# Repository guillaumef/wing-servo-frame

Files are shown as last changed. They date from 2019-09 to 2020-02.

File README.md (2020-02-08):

# wing-servo-frame

Wing servo frame - fully parametric - arms/bearing - servo database

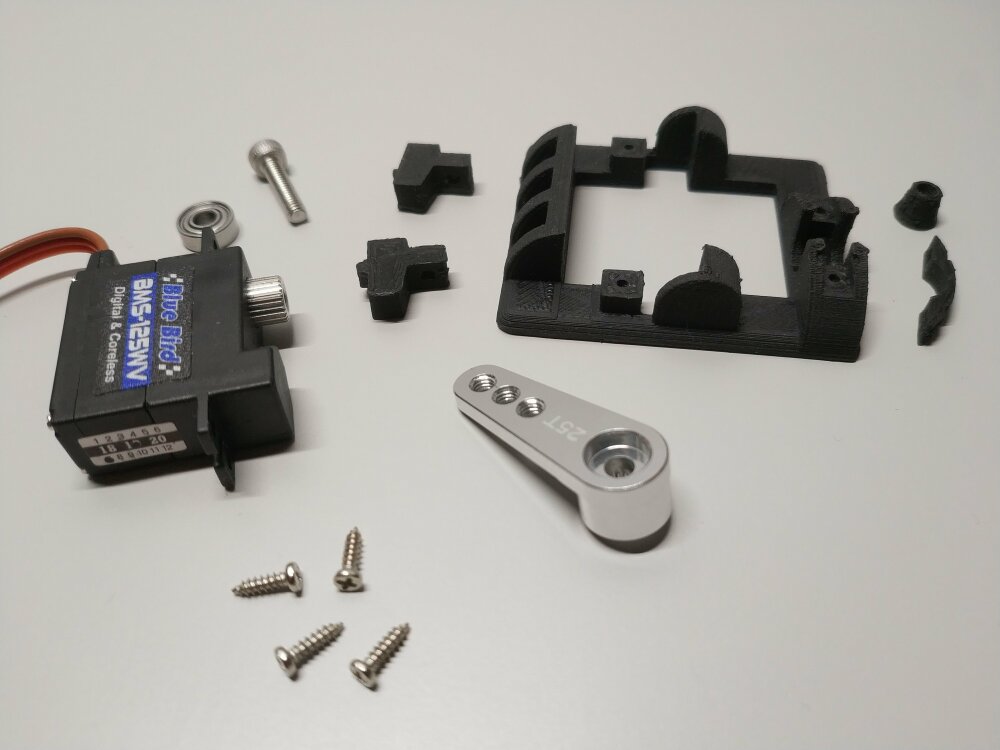
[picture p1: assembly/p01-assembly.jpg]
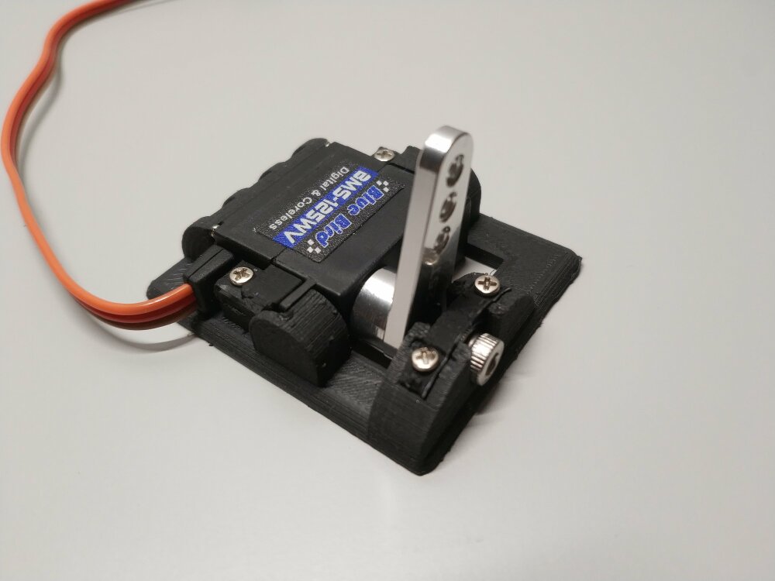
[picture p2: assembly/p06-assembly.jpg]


Videos (KST X08N, Bluebird BMS-125WV):

[](https://youtu.be/2ph3OZgdkxs) [](https://youtu.be/XQHXTqi7j4g)

[All animated gifs](GIFSHOW.md)

### Project description

- all servo ears format
- parametric servo dimensions
- parametric bearing dimensions (like: MR83ZZ -> MR95ZZ ...)
- with or without external bearing (also with parametric bearing dimensions), left/right/both sides
- for horizontal ears, manage ear notch, screws or both
- many options (general thickness, arm clearance, frame round factor, mode light, ...)
- no added height to the servo thickness

### Directories/files

- servo-frame.scad : OpenScad code and embedded documentation
- configuration.scad : Configuration and constants with embedded documentation
- Makefile : generate the STLs for all known servos
- stls : some auto-generated STLs for each servo in the KB (in some configurations)
- assembly : pictures and video of the assembly

### Usage

You need openscad and a text editor.

```
git clone https://github.com/guillaumef/wing-servo-frame.git
```

- Launch openscad on servo-frame.scad
- Edit the configuration.scad file to fit your needs (openscad preview can be a bit tricked by the complexity, use F6 to render the final version if necessary)
- Generate the STL
- Print...

### Bearing and screw

Both are easy to find, portable and far more cost-effective than commercial products and
proprietary arm screws.

The trivial constraint:
screw diameter (servo arm screw) must be inferior or equal to the bearing internal diameter.

##### Screw

The arm screw is replaced with a longer one.

Nearly all servo arm screws are M2,M2.5,M3.
A dissident is the KST X12, with M2.3 screw (nearly proprietary).
For this one, the simpliest way is a M2.5 tap set (flat tip or make it flatter), you get a strong M2.5 with 3.5mm depth.
You need M2,M2.5,M3 screws with a minimum length of 15mm and you are good to go for any servos.

##### Bearing

The scad file is generating the specified servo arm clearance (space between the
arm and the frame).
It is also generating the bearing shaft except for two special modes:
- if screw diameter is equal to bearing internal diameter: screw is automatically use as bearing shaft
- if screw head diameter is equal to bearing internal diameter: screw head is automatically use as bearing shaft

Bearing price is $2 for 10pcs, $8 for 50pcs... (aliexpress).

The servo frame accepts 8mm bearing even for 8mm servo.

To manage any kind of servos, choose your way:
- To get a full steel shaft, buy a bunch of them with 2mm,2.5mm,3mmm internal diameter. i.e:
  - MR52ZZ (2x5x2.5 mm)
  - 682XZZ (2.5x6x2.6 mm)
  - MR63ZZ (3x6x2.5 mm)
- To get a printed shaft, buy a bunch of 5mm internal diameter. i.e:
  - MR85ZZ (5x8x2.5)

### STLs directory

To ease the process, this directory provides multiple automatically generated STLs in some configurations:
- hollow / solid frame
- bearing: none/left/right/both

The configuration file is provided for each generated stl.
The bearing size is chosen for the best case scenario per servo: screw as the bearing shaft.

### Openscad feedback

The scad file is providing you information feedback on the screw/bearing.
Like this one:
```
ECHO: "******************"
ECHO: "Bearing shaft/arm screw:"
ECHO: "**** the shaft inserted in the bearing is printed"
ECHO: "**** screw length (threaded part) should be approximately between 15.5 and 18.3 mm"
ECHO: "**** >> Tuning the length is possible with the 'frame_arm_clearance' parameter"
ECHO: "**** screw thread metric is M3"
ECHO: "******************"
```
Or:
```
ECHO: "******************"
ECHO: "Bearing shaft/arm screw:"
ECHO: "**** 'arm_screw_dia' matches bearing internal diameter:"
ECHO: "**** >> the screw is the bearing shaft"
ECHO: "**** screw length (threaded part) should be approximately between 14.5 and 17.3 mm"
ECHO: "**** >> Tuning the length is possible with the 'frame_arm_clearance' parameter"
ECHO: "**** screw thread metric is M3"
ECHO: "******************"
```

##### Printing

100% infill, ABS or Nylon material. Small layer printing is better.
On a Ultimaker2, ~ one servo frame per hour in good quality (layer 0.1mm).

### Miscellaneous

- on carbon/fiberglass, use coarse grit sandpaper to roughen up the surfaces and
clean with acetone (NEVER on ABS)
- use a thread-locking fluid for the arm screw.
- for wings, add a strap (1-2mm Fiberglass, carbon) between the wing
top skin and the servo/frame. I quote the "Aeroic Schwing instructions":
This all ensures a ridgedly held servo. Servos that pop off do so because of flex in
the skins. Doing it this way there’s a lot of gluing area and no flex so the servo
cannot pop off. A weak glue joint with an unprepared servo is perfectly adequate.
The servo is held on the top skin, bottom skin and the head is held by the bearing
housing which itself is bonded to both skins! To remove just cut the strap, unbolt
the shaft and twist the servo. It pops out clean! But most of the time it may be you
just need to replace the arm. Then it’s even easier as you just unbolt the shaft and
leave the servo in situ.

### Servo database

If you add new servo dimensions to the list, I will be pleased to include them.
You can provide them via a Github Issue. Thanks!

Servo list:

- MKS DS6100 / HV6100
- MKS DS75K
- MKS DS75K-N
- MKS HV6130
- BlueBird BMS-125WV / BMS-126WV / BMS-127WV
- BlueBird BMS-207WV
- BlueBird BMS-115HV
- BlueBird BMS-A10S
- BlueBird BMS-A10V
- BlueBird BMS-A10H
- KST X12-508 HV
- KST X10 HV / DS125MG / DS225MG
- KST X10 MINI HV / DS135MG
- KST X10-710 HV / DS145MG
- KST X08 HV
- KST X08H HV
- KST X08N HV
- KST X08 Plus HV
- KST X08H Plus HV
- Emax ES3352
- Emax ES08MDII
- TowerPro MG90D 15g

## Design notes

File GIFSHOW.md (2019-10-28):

## BlueBird-BMS-115HV

#### hollow
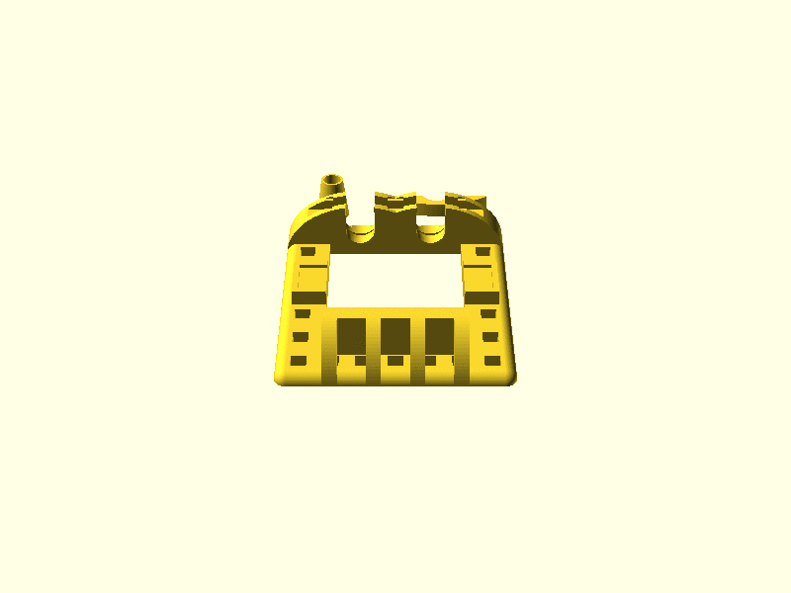
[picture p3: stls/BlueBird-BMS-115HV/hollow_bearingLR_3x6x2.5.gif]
BlueBird-BMS-115HV frame
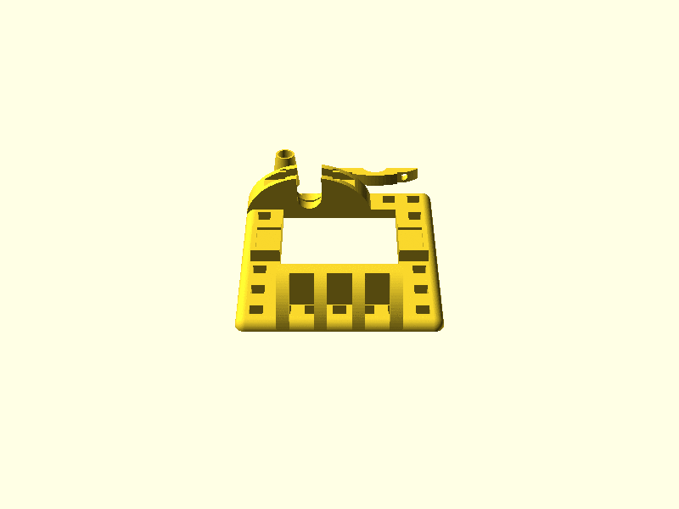
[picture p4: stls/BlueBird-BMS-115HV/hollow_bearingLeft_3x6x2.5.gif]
BlueBird-BMS-115HV frame
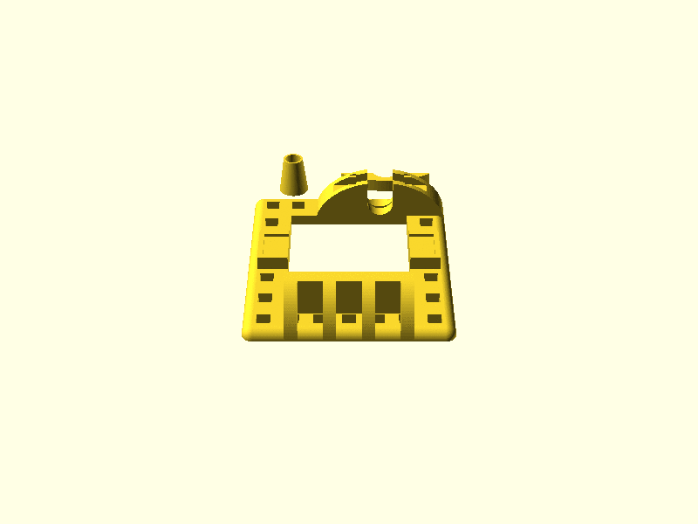
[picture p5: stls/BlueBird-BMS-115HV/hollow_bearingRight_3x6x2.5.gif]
BlueBird-BMS-115HV frame
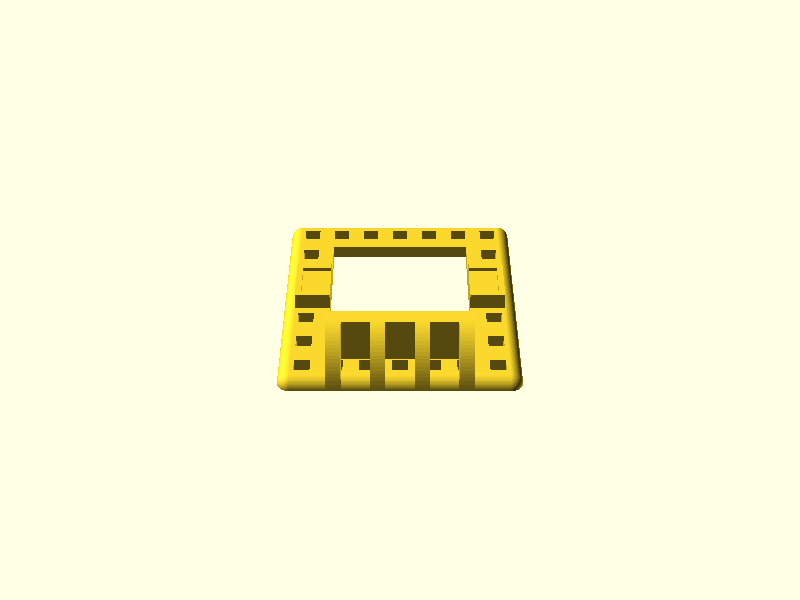
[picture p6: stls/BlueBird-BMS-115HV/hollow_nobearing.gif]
BlueBird-BMS-115HV frame
    
#### solid
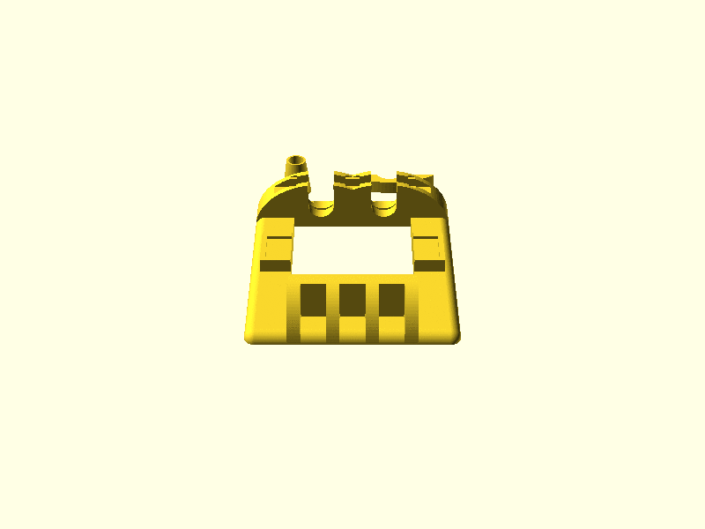
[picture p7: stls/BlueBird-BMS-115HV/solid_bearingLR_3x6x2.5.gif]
BlueBird-BMS-115HV frame
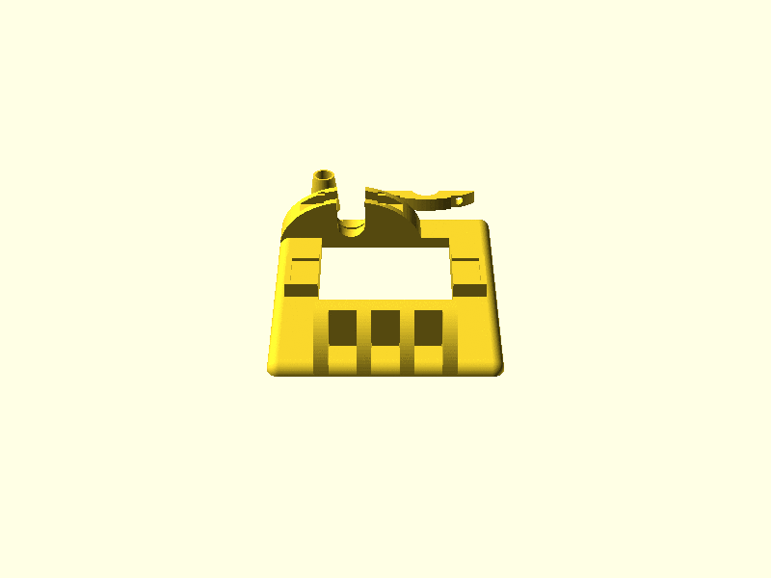
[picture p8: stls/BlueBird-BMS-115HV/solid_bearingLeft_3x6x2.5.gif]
BlueBird-BMS-115HV frame
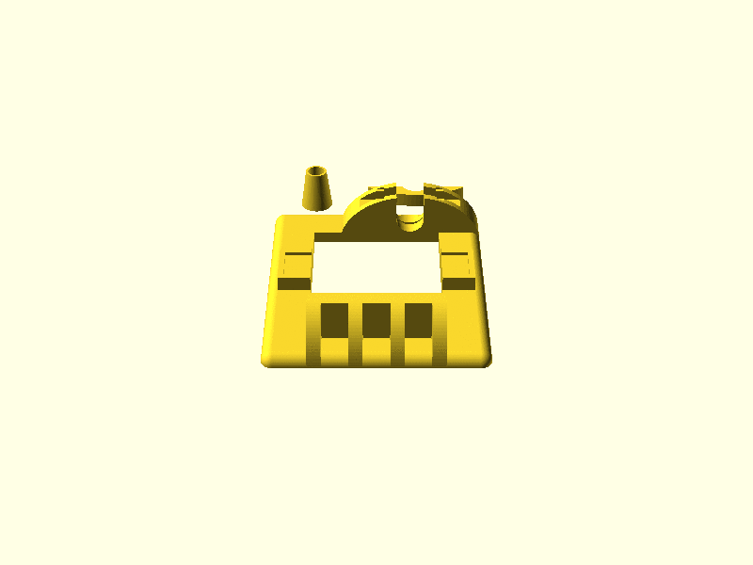
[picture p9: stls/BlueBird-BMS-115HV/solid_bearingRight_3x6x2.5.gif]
BlueBird-BMS-115HV frame
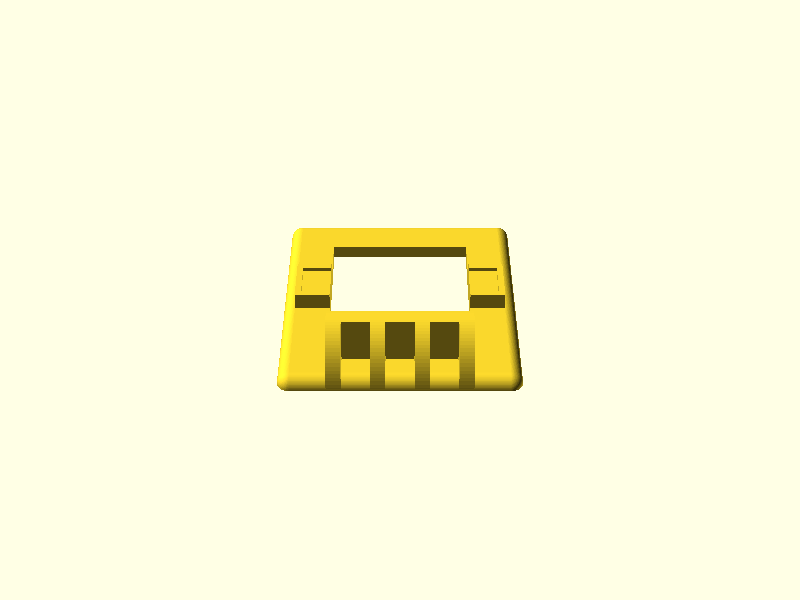
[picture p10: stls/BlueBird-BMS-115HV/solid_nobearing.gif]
BlueBird-BMS-115HV frame
    

## BlueBird-BMS-125WV

#### hollow
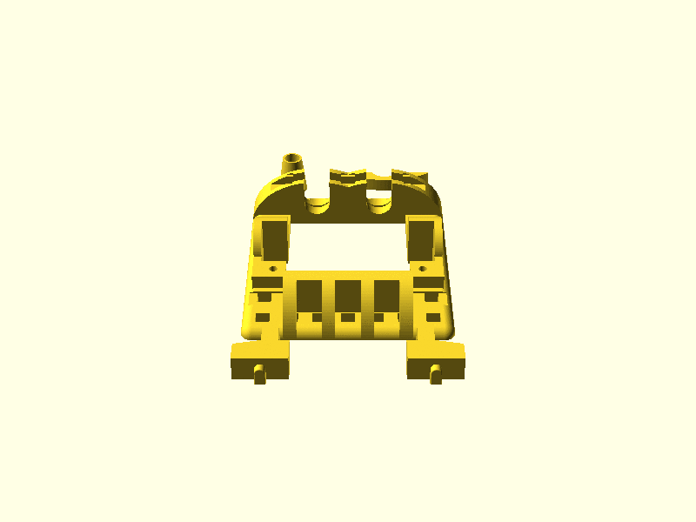
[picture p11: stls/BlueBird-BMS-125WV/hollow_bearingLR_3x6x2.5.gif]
BlueBird-BMS-125WV frame
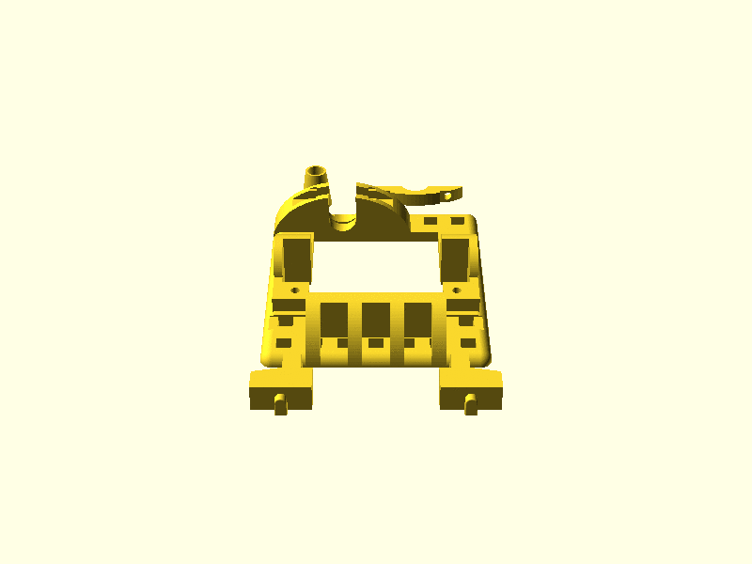
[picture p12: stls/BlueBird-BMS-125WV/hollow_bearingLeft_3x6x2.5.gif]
BlueBird-BMS-125WV frame
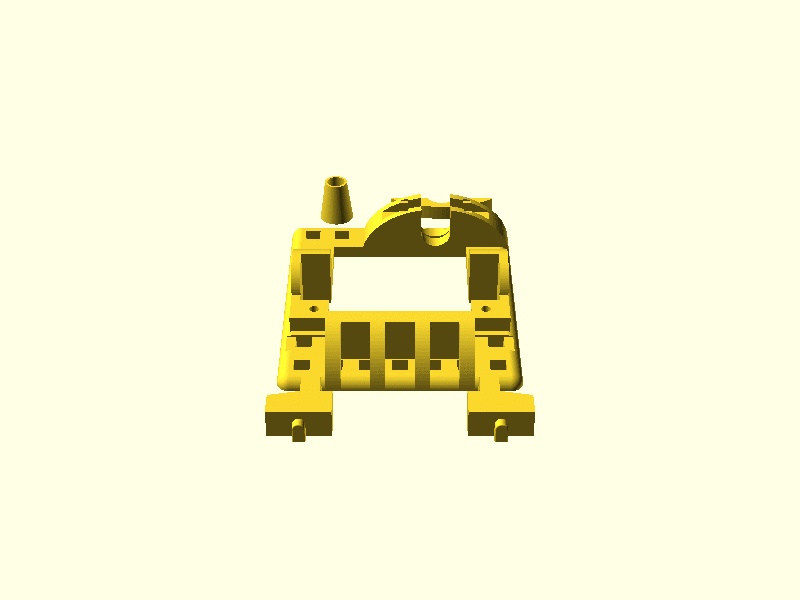
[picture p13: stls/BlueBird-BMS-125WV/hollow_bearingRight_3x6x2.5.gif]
BlueBird-BMS-125WV frame
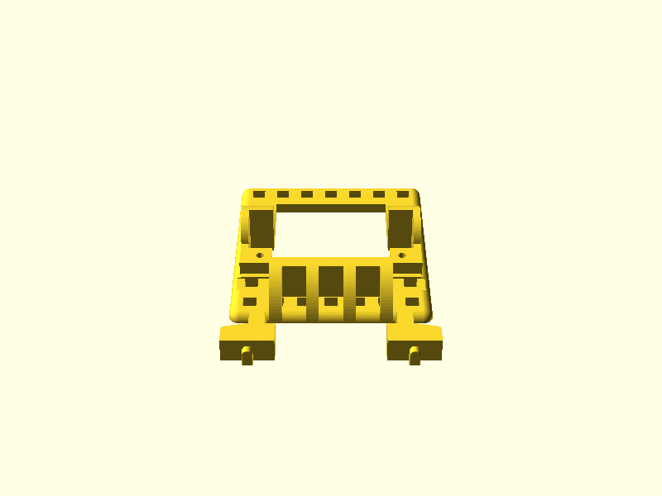
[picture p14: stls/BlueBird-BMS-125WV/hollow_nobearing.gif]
BlueBird-BMS-125WV frame
    
#### solid
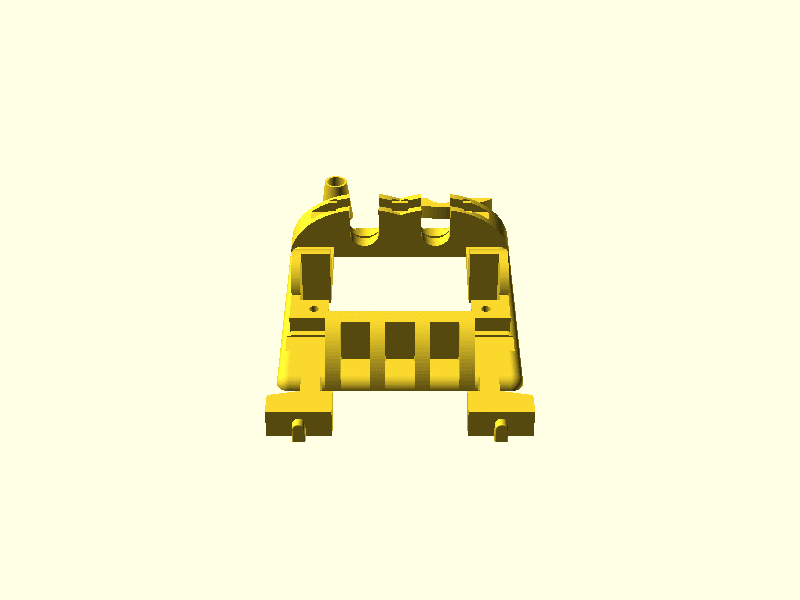
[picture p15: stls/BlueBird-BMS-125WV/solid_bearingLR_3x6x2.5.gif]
BlueBird-BMS-125WV frame
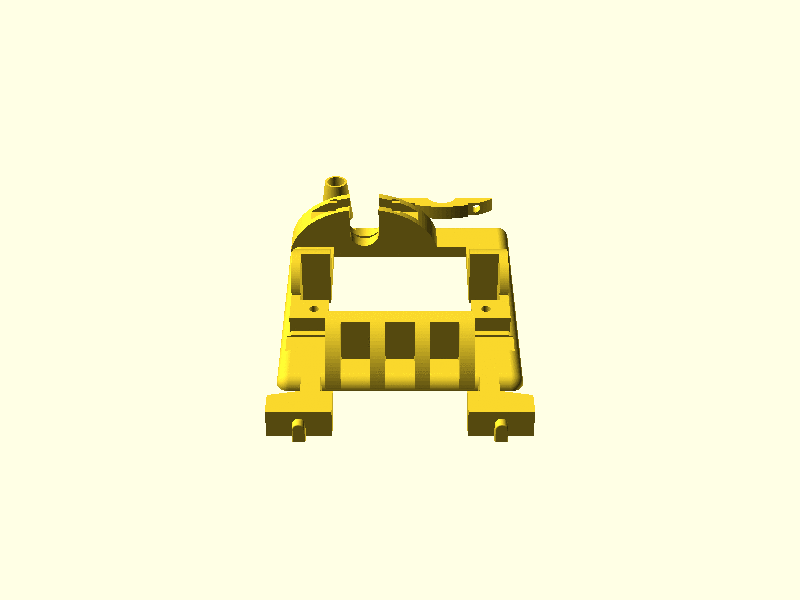
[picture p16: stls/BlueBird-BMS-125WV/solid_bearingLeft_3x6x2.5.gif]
BlueBird-BMS-125WV frame
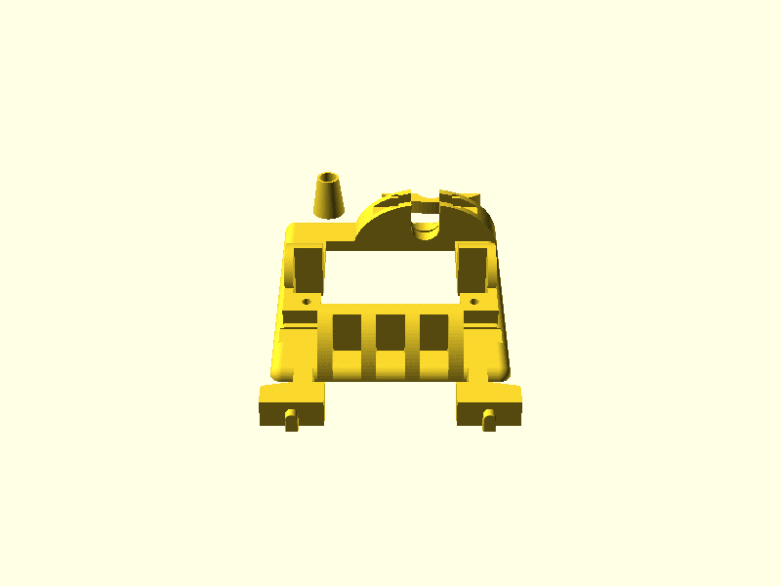
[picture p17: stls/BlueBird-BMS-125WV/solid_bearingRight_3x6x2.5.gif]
BlueBird-BMS-125WV frame
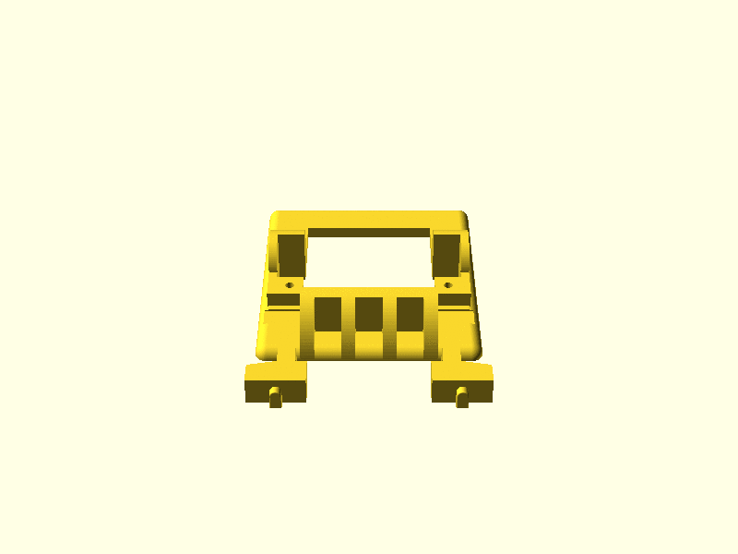
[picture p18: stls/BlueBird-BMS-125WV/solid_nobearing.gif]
BlueBird-BMS-125WV frame
    

## BlueBird-BMS-207WV

#### hollow
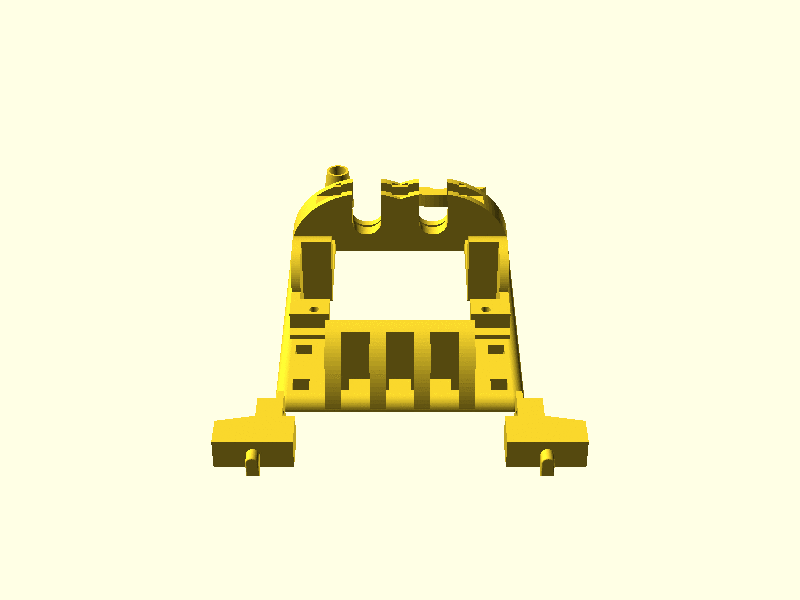
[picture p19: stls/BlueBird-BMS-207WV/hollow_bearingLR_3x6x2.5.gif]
BlueBird-BMS-207WV frame
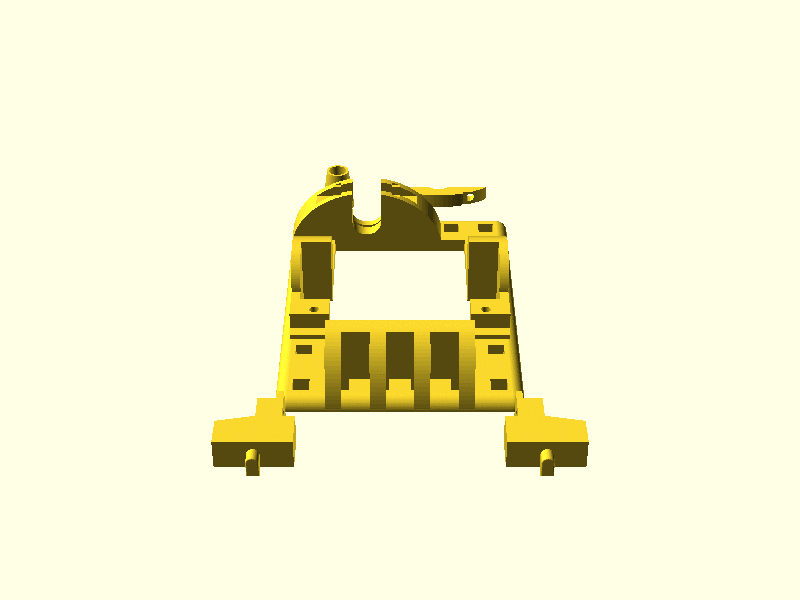
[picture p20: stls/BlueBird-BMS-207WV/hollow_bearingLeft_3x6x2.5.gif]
BlueBird-BMS-207WV frame
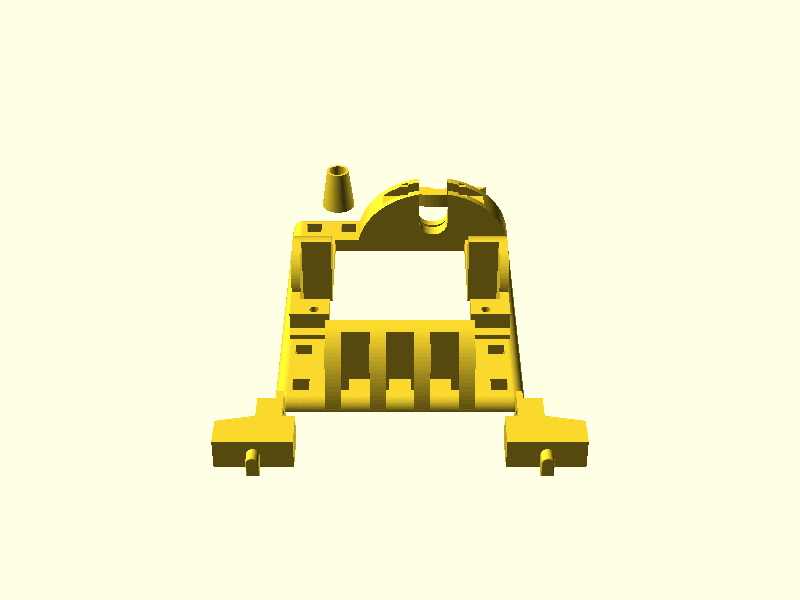
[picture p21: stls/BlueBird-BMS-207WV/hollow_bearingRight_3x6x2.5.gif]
BlueBird-BMS-207WV frame
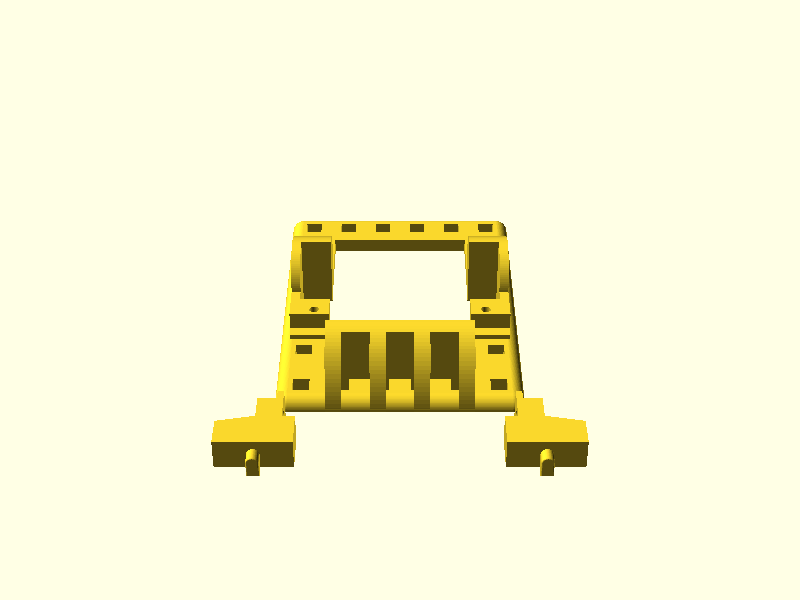
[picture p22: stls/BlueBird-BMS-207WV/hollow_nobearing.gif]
BlueBird-BMS-207WV frame
    
#### solid
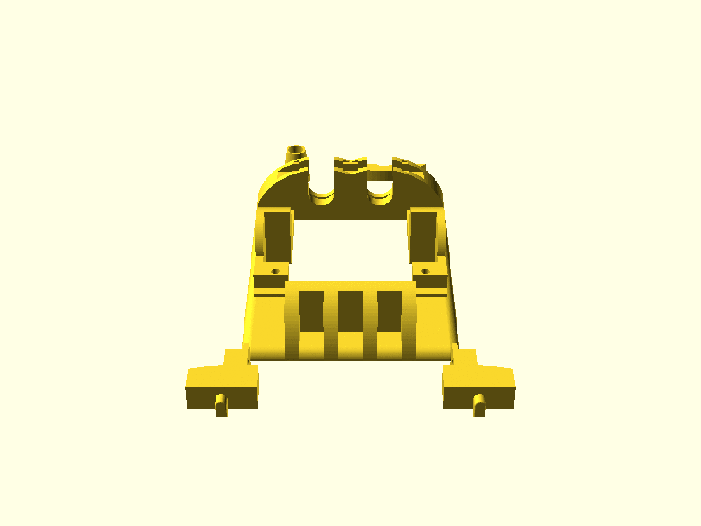
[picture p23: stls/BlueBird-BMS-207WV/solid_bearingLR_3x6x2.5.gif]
BlueBird-BMS-207WV frame
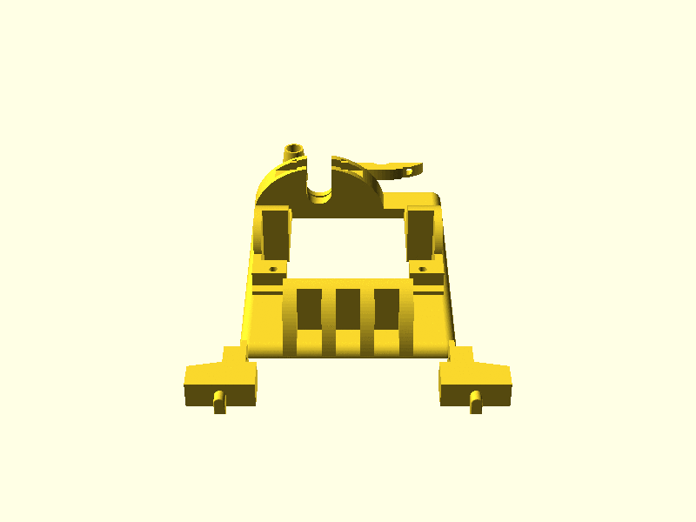
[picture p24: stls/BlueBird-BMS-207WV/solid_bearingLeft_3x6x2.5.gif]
BlueBird-BMS-207WV frame
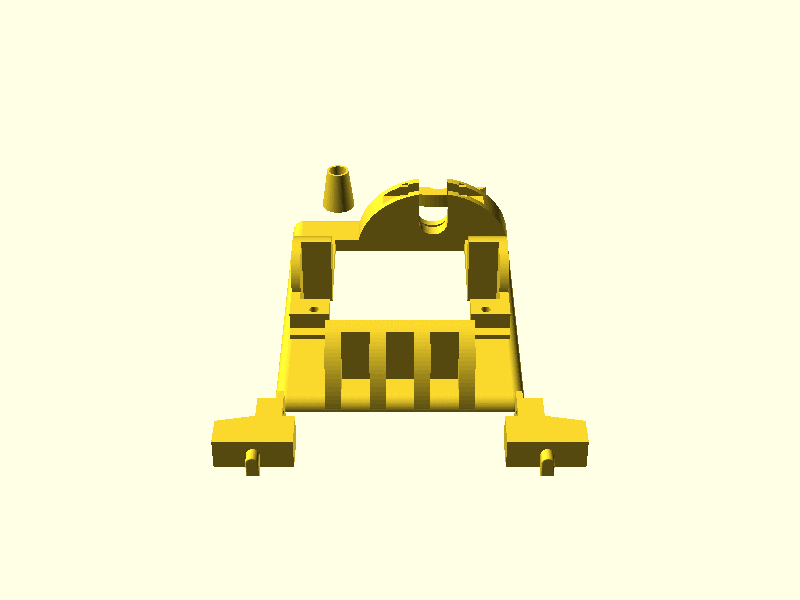
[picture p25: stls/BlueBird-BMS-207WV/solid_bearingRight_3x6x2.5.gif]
BlueBird-BMS-207WV frame
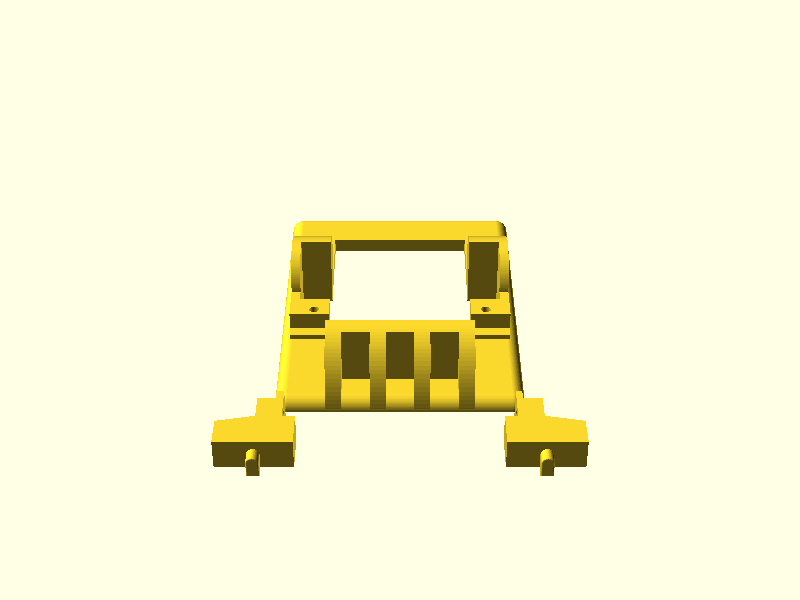
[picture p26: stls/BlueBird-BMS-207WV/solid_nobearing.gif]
BlueBird-BMS-207WV frame
    

## BlueBird-BMS-A10H

#### hollow
BlueBird-BMS-A10H frame BlueBird-BMS-A10H frame BlueBird-BMS-A10H frame BlueBird-BMS-A10H frame 
#### solid
BlueBird-BMS-A10H frame BlueBird-BMS-A10H frame BlueBird-BMS-A10H frame BlueBird-BMS-A10H frame 

## BlueBird-BMS-A10S

#### hollow
BlueBird-BMS-A10S frame BlueBird-BMS-A10S frame BlueBird-BMS-A10S frame BlueBird-BMS-A10S frame 
#### solid
BlueBird-BMS-A10S frame BlueBird-BMS-A10S frame BlueBird-BMS-A10S frame BlueBird-BMS-A10S frame 

## BlueBird-BMS-A10V

#### hollow
BlueBird-BMS-A10V frame BlueBird-BMS-A10V frame BlueBird-BMS-A10V frame BlueBird-BMS-A10V frame 
#### solid
BlueBird-BMS-A10V frame BlueBird-BMS-A10V frame BlueBird-BMS-A10V frame BlueBird-BMS-A10V frame 

## Emax-ES08MDII

#### hollow
Emax-ES08MDII frame Emax-ES08MDII frame Emax-ES08MDII frame Emax-ES08MDII frame 
#### solid
Emax-ES08MDII frame Emax-ES08MDII frame Emax-ES08MDII frame Emax-ES08MDII frame 

## Emax-ES3352

#### hollow
Emax-ES3352 frame Emax-ES3352 frame Emax-ES3352 frame Emax-ES3352 frame 
#### solid
Emax-ES3352 frame Emax-ES3352 frame Emax-ES3352 frame Emax-ES3352 frame 

## KST-X08-HV

#### hollow
KST-X08-HV frame KST-X08-HV frame KST-X08-HV frame KST-X08-HV frame 
#### solid
KST-X08-HV frame KST-X08-HV frame KST-X08-HV frame KST-X08-HV frame 

## KST-X08-Plus-HV

#### hollow
KST-X08-Plus-HV frame KST-X08-Plus-HV frame KST-X08-Plus-HV frame KST-X08-Plus-HV frame 
#### solid
KST-X08-Plus-HV frame KST-X08-Plus-HV frame KST-X08-Plus-HV frame KST-X08-Plus-HV frame 

## KST-X08H-HV

#### hollow
KST-X08H-HV frame KST-X08H-HV frame KST-X08H-HV frame KST-X08H-HV frame 
#### solid
KST-X08H-HV frame KST-X08H-HV frame KST-X08H-HV frame KST-X08H-HV frame 

## KST-X08H-Plus-HV

#### hollow
KST-X08H-Plus-HV frame KST-X08H-Plus-HV frame KST-X08H-Plus-HV frame KST-X08H-Plus-HV frame 
#### solid
KST-X08H-Plus-HV frame KST-X08H-Plus-HV frame KST-X08H-Plus-HV frame KST-X08H-Plus-HV frame 

## KST-X08N-HV

#### hollow
KST-X08N-HV frame KST-X08N-HV frame KST-X08N-HV frame KST-X08N-HV frame 
#### solid
KST-X08N-HV frame KST-X08N-HV frame KST-X08N-HV frame KST-X08N-HV frame 

## KST-X10-710-HV

#### hollow
KST-X10-710-HV frame KST-X10-710-HV frame KST-X10-710-HV frame KST-X10-710-HV frame 
#### solid
KST-X10-710-HV frame KST-X10-710-HV frame KST-X10-710-HV frame KST-X10-710-HV frame 

## KST-X10-HV

#### hollow
KST-X10-HV frame KST-X10-HV frame KST-X10-HV frame KST-X10-HV frame 
#### solid
KST-X10-HV frame KST-X10-HV frame KST-X10-HV frame KST-X10-HV frame 

## KST-X10-MINI-HV

#### hollow
KST-X10-MINI-HV frame KST-X10-MINI-HV frame KST-X10-MINI-HV frame KST-X10-MINI-HV frame 
#### solid
KST-X10-MINI-HV frame KST-X10-MINI-HV frame KST-X10-MINI-HV frame KST-X10-MINI-HV frame 

## KST-X12-508-HV

#### hollow
KST-X12-508-HV frame KST-X12-508-HV frame KST-X12-508-HV frame KST-X12-508-HV frame 
#### solid
KST-X12-508-HV frame KST-X12-508-HV frame KST-X12-508-HV frame KST-X12-508-HV frame 

## MKS-DS6100

#### hollow
MKS-DS6100 frame MKS-DS6100 frame MKS-DS6100 frame MKS-DS6100 frame 
#### solid
MKS-DS6100 frame MKS-DS6100 frame MKS-DS6100 frame MKS-DS6100 frame 

## MKS-DS75K-N

#### hollow
MKS-DS75K-N frame MKS-DS75K-N frame MKS-DS75K-N frame MKS-DS75K-N frame 
#### solid
MKS-DS75K-N frame MKS-DS75K-N frame MKS-DS75K-N frame MKS-DS75K-N frame 

## MKS-DS75K

#### hollow
MKS-DS75K frame MKS-DS75K frame MKS-DS75K frame MKS-DS75K frame 
#### solid
MKS-DS75K frame MKS-DS75K frame MKS-DS75K frame MKS-DS75K frame 

## MKS-HV6130

#### hollow
MKS-HV6130 frame MKS-HV6130 frame MKS-HV6130 frame MKS-HV6130 frame 
#### solid
MKS-HV6130 frame MKS-HV6130 frame MKS-HV6130 frame MKS-HV6130 frame 

## TowerPro-MG90D-15g

#### hollow
TowerPro-MG90D-15g frame TowerPro-MG90D-15g frame TowerPro-MG90D-15g frame TowerPro-MG90D-15g frame 
#### solid
TowerPro-MG90D-15g frame TowerPro-MG90D-15g frame TowerPro-MG90D-15g frame TowerPro-MG90D-15g frame

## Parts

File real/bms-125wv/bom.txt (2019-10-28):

1 x BlueBird BMS-125WV
   ...

1 x MR63ZZ - aliexpress
1 x M3*16 - aliexpress
1 x Servo arm 25T Metal - aliexpress
4 x mini screws for wood/abs - classic micro servo screws

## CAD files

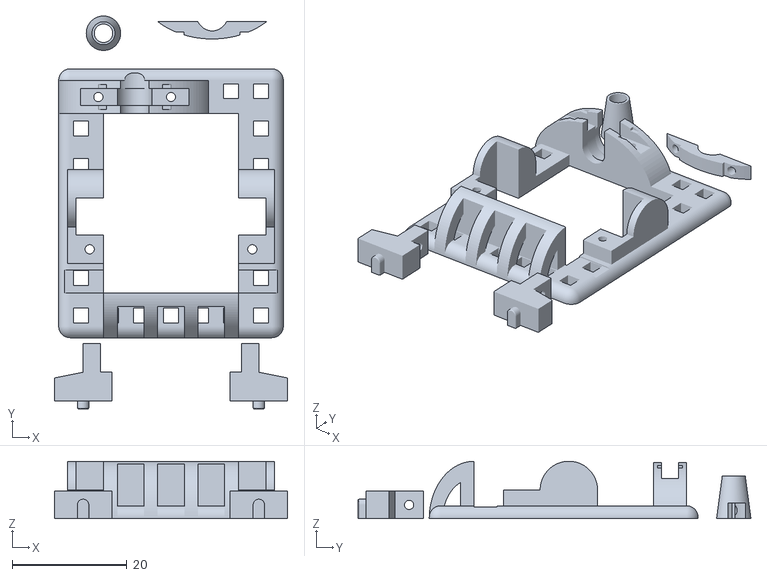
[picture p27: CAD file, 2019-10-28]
real/bms-125wv/model.stl
40.6 x 68.4 x 10.0

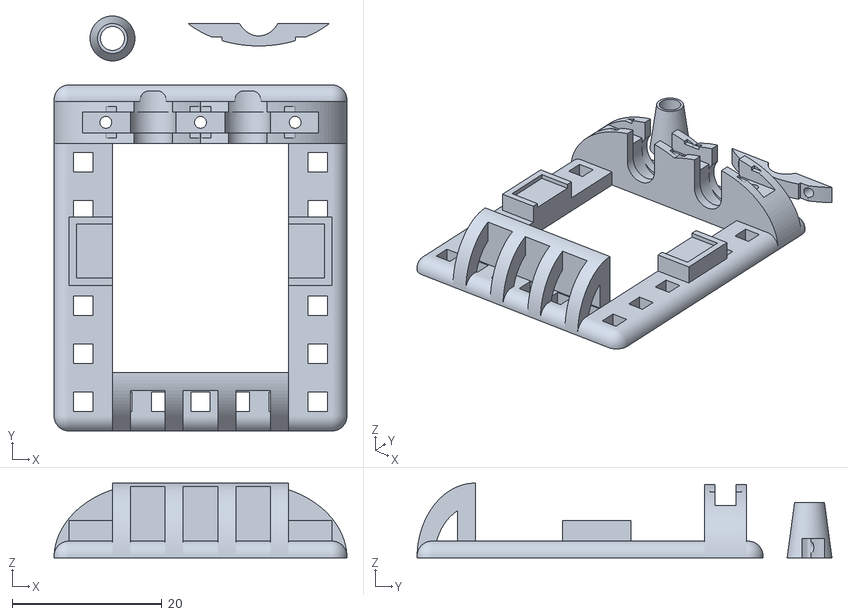
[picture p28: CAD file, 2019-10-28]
stls/BlueBird-BMS-115HV/hollow_bearingLR_3x6x2.5.stl
39.1 x 55.4 x 10.0

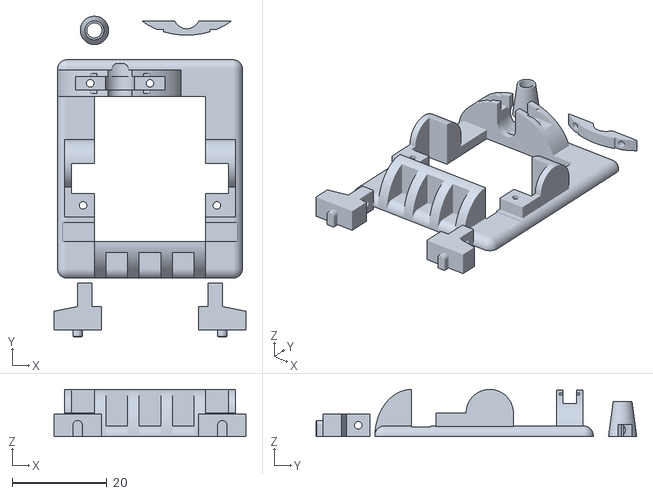
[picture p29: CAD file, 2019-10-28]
stls/BlueBird-BMS-125WV/solid_bearingLeft_3x6x2.5.stl
40.6 x 67.8 x 10.0

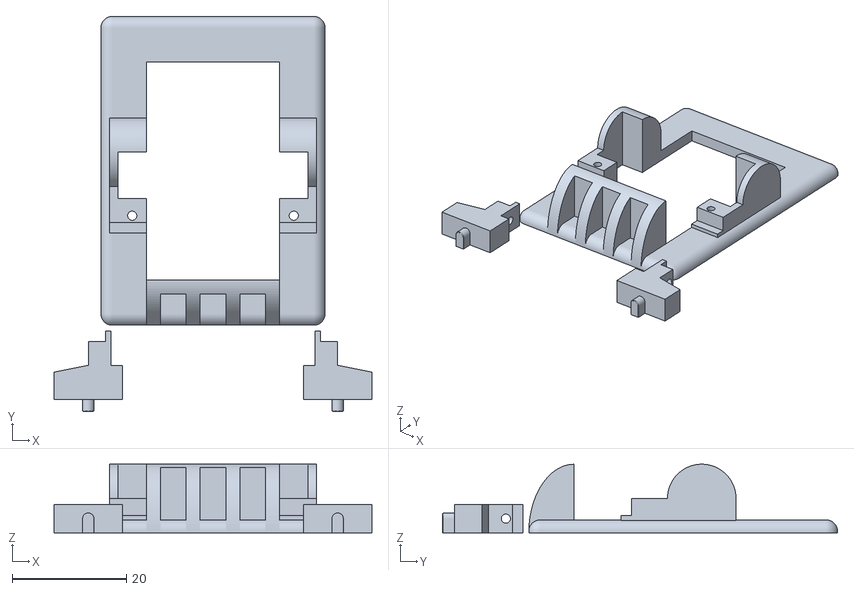
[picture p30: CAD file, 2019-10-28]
stls/BlueBird-BMS-207WV/solid_nobearing.stl
55.6 x 69.1 x 12.0

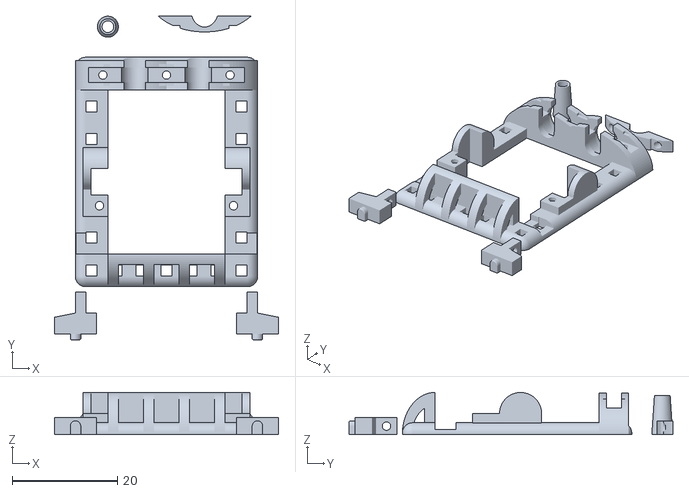
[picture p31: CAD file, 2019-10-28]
stls/BlueBird-BMS-A10H/hollow_bearingLR_2x5x2.5.stl
42.6 x 61.5 x 8.00

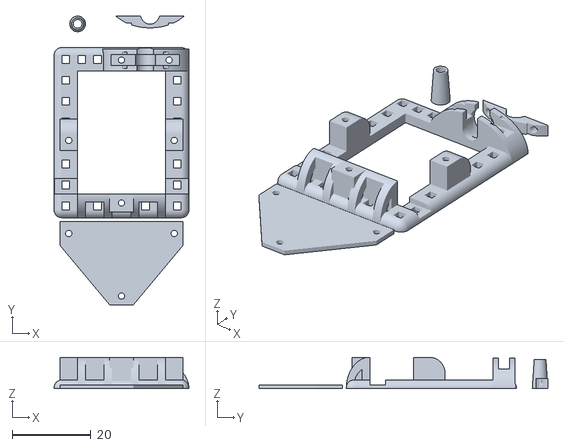
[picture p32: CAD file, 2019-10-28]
stls/BlueBird-BMS-A10S/hollow_bearingRight_2x5x2.5.stl
34.3 x 73.4 x 8.00

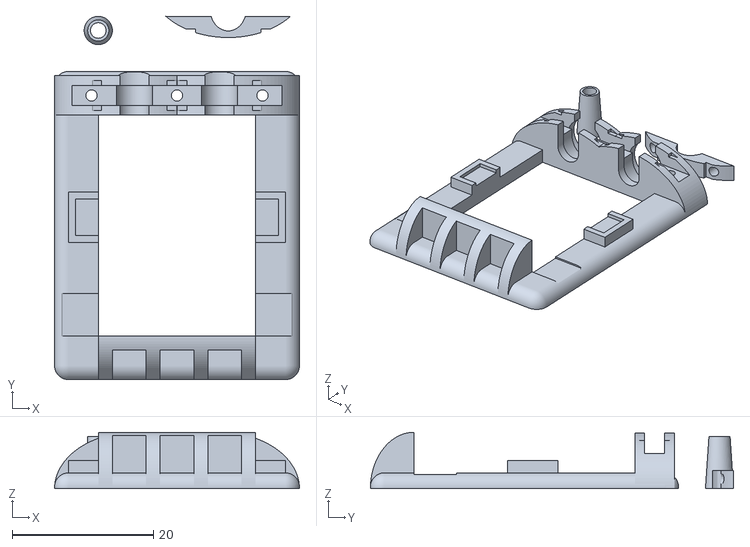
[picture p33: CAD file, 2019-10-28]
stls/BlueBird-BMS-A10V/solid_bearingLR_2x5x2.5.stl
34.7 x 51.5 x 8.00

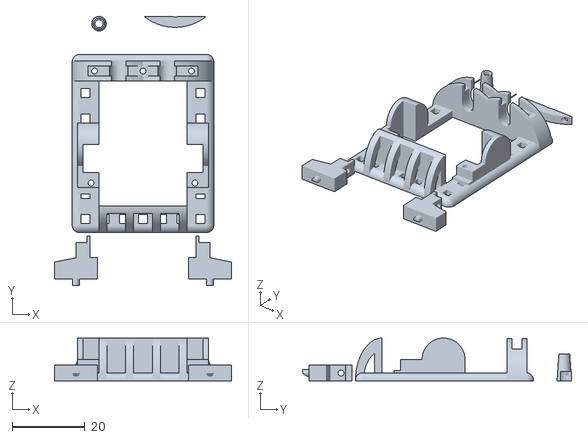
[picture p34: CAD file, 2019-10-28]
stls/Emax-ES08MDII/hollow_bearingLR_2x5x2.5.stl
48.6 x 73.9 x 11.8

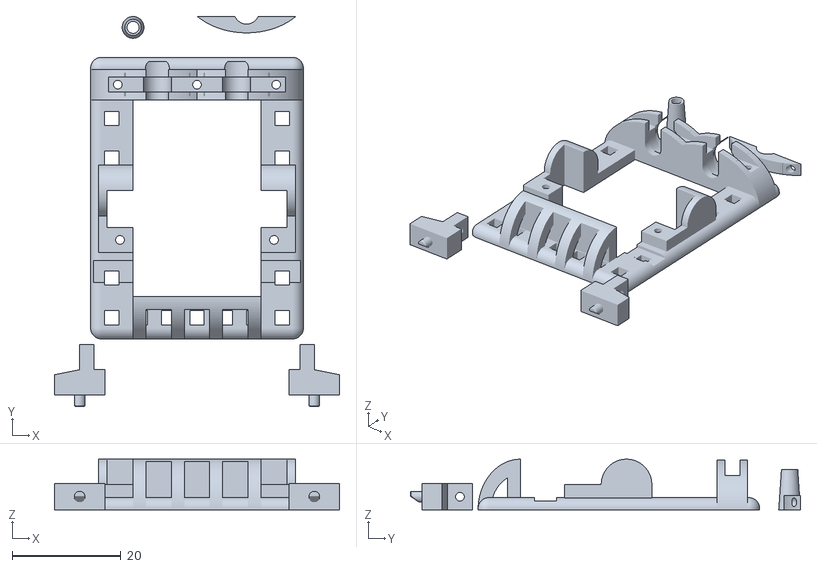
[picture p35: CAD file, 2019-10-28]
stls/Emax-ES3352/hollow_bearingLR_2x5x2.5.stl
52.4 x 71.6 x 9.30

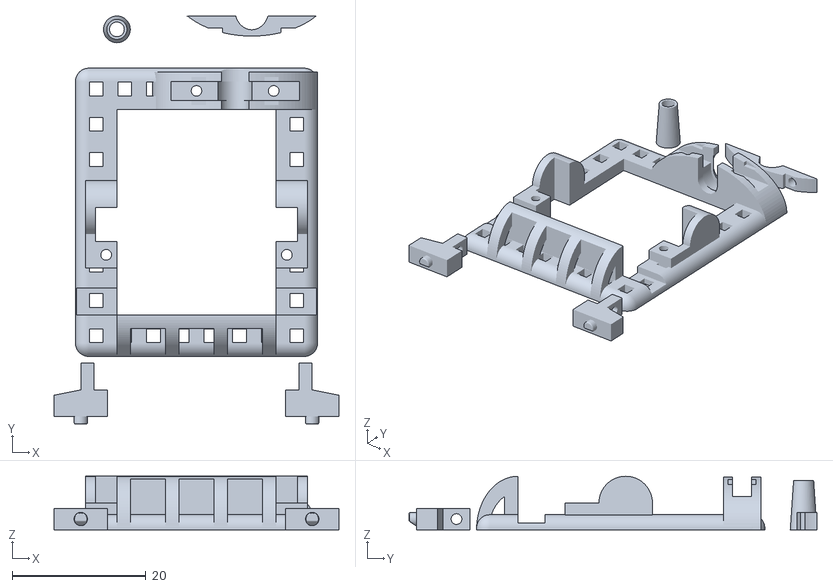
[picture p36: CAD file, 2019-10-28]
stls/KST-X08-HV/hollow_bearingRight_2x5x2.5.stl
42.6 x 61.0 x 8.00

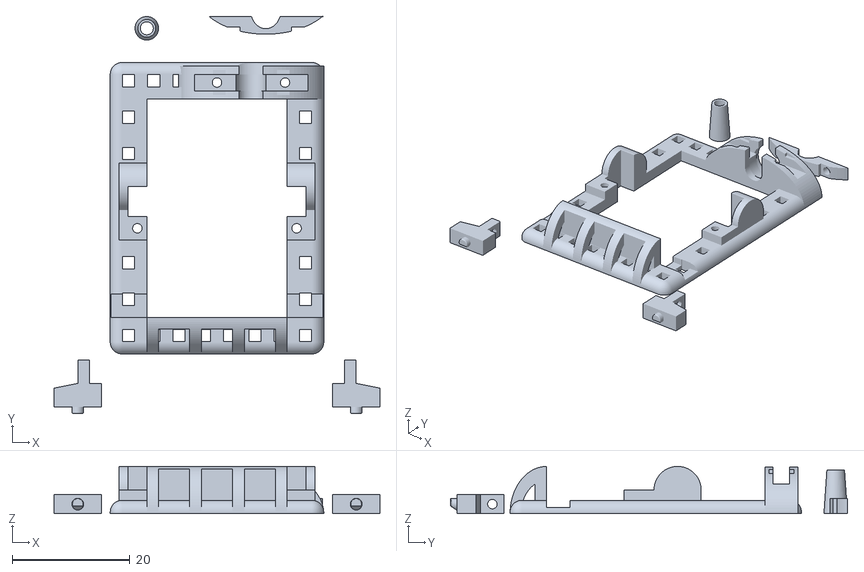
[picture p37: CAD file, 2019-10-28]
stls/KST-X08-Plus-HV/hollow_bearingRight_2x5x2.5.stl
55.2 x 67.3 x 8.00

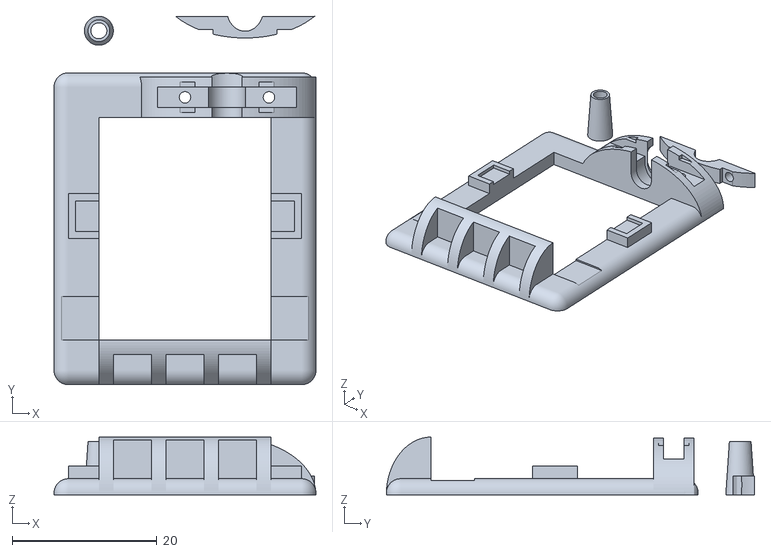
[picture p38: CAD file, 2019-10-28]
stls/KST-X08H-HV/solid_bearingRight_2x5x2.5.stl
36.2 x 50.9 x 8.00

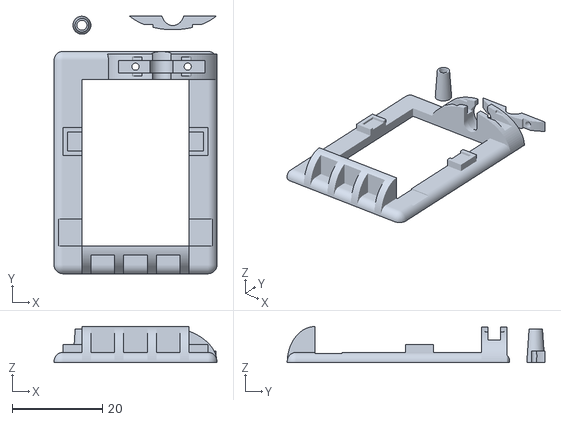
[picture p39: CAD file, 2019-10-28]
stls/KST-X08H-Plus-HV/solid_bearingRight_2x5x2.5.stl
36.2 x 57.2 x 8.00

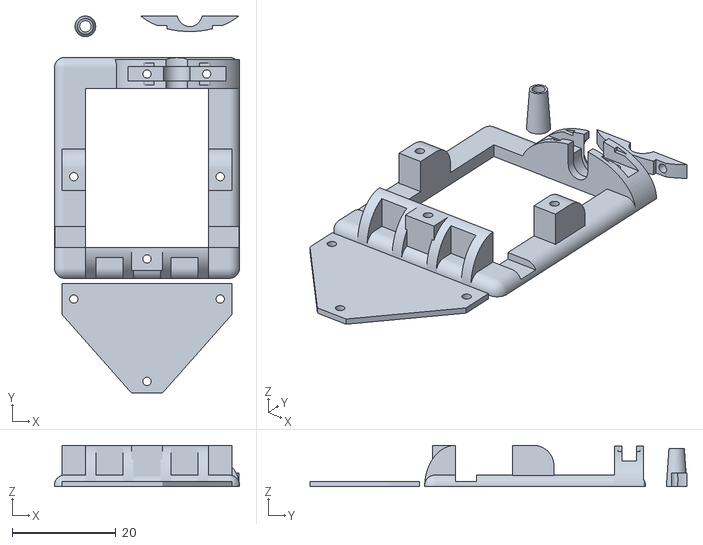
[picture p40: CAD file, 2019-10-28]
stls/KST-X08N-HV/solid_bearingRight_2x5x2.5.stl
35.8 x 72.8 x 8.00

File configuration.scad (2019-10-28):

/*
 *
 * Wing Servo Frame configuration
 *
 */

servo_id	= [ 1 , 0 ];   /* Brand,Servo  - list in servo-frame.scad */

bearing_id	= 2;           /* Bearing id   - list in servo-frame.scad */


/*
   Options - External to servo dimensions
 */

/* Ears properties */

ear_support_screw	= 1;	/* for LEG_FORMAT=1, manage L-shaped block vertically screwed on
				 * the servo frame
				 * Modes:
				 *
				 *   0: no z-axis locking - classic for wing bottom skin strap mount
				 *   1: with a central notch in servo ear
				 *   2: with screws in servo ear
				 *   3: 1&2
				 *
				 */
ear_support_screwhead	= 3;	/* with ear_support_screw == 2, diameter of the screw head */

z_axis_servo_cover	= 1;	/* with ear_support_screw == 0, make a servo cover */


/* Servo arm properties */

arm_thickness		= .5;	/* It is the added thickness of the servo arm between the
				 * arm screw head (top of the threaded part) and the servo gear.
				 *
				 * With plastic arm, often low thickness, like .5 ~ 1 mm
				 * With aluminium arm, often higher thickness, like 1 ~ 2.5 mm
				 *
				 * If you don't know, take a secure value of .5mm so you will be
				 * able to trim/sand down the cone part if it is too big.
				 *
				 * You have to consider the servo arm height part which is covering
				 * the screw head and add it to the "frame_arm_clearance".
				 */

arm_screw_head_dia	= 5.5;	/* (needed if 'with_bearing')
				 *
				 * 2 cases:
				 *
				 * - arm_screw_head_dia == bearing internal diameter
				 *    The screw head is used directly in the bearing
				 *    The bearing shaft produced is a spacer
				 *    to lock the servo arm in place.
				 *    => shorted screw needed.
				 *
				 * - arm_screw_head_dia != bearing internal diameter
				 *    The screw head is locking the bearing shaft externally.
				 *    The bearing shaft produced is entering in the bearing.
				 *    => longer screw needed.
				 *
				 */

/* Frame properties */

frame_thickness		= 1.5; 	/* thickness of the frame */

frame_extra_width	= 3.0; 	/* extra width of the frame */

frame_arm_clearance	= 6;    /* clearance between the servo arm top (arm screw hole)
				 * and the start of the servo frame top
				 * (aka bearing support if 'with_bearing').
				 *
				 * See also 'arm_thickness' definition.
				 *
				 * if 'with_bearing', this frame arm clearance is going to
				 * define the Arm screw length.
				 * In the console of openscad, for the current parameters,
				 * the arm screw length needed is displayed.
				 */

frame_mode_light	= 1;	/* 0: solid frame
				 * 1: make holes in frame: lighter and probably enhance gluing
				 */

/* Bearing properties */

with_bearing 		= 1; 	/* 0: no bearing
				 * 1: With shaft bearing - Right
				 * 2: With shaft bearing - Left
				 * 3: With shaft bearing - Both - universal
				 */

/* MISC */

minkowski_rounded 	= 2;	/* rounded frame sphere */

$fn 			= 100;  /* Global circles segment number: 30 for design, >=100 for STL */

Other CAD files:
stls/KST-X10-710-HV/hollow_bearingRight_2.5x6x2.6.stl
stls/KST-X10-HV/hollow_bearingRight_2.5x6x2.6.stl
stls/KST-X10-MINI-HV/solid_bearingRight_2.5x6x2.6.stl
stls/KST-X12-508-HV/solid_bearingLR_2.5x6x2.6.stl
real/bms-125wv/configuration.scad
stls/BlueBird-BMS-115HV/hollow_bearingLeft_3x6x2.5.configuration.scad
stls/BlueBird-BMS-115HV/hollow_bearingLR_3x6x2.5.configuration.scad
servo-frame.scad
stls/BlueBird-BMS-115HV/hollow_bearingLeft_3x6x2.5.stl
stls/BlueBird-BMS-115HV/hollow_bearingRight_3x6x2.5.configuration.scad
stls/BlueBird-BMS-115HV/hollow_bearingRight_3x6x2.5.stl
stls/BlueBird-BMS-115HV/hollow_nobearing.configuration.scad
stls/BlueBird-BMS-115HV/hollow_nobearing.stl
stls/BlueBird-BMS-115HV/solid_bearingLR_3x6x2.5.configuration.scad
stls/BlueBird-BMS-115HV/solid_bearingLR_3x6x2.5.stl
stls/BlueBird-BMS-115HV/solid_bearingLeft_3x6x2.5.configuration.scad
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

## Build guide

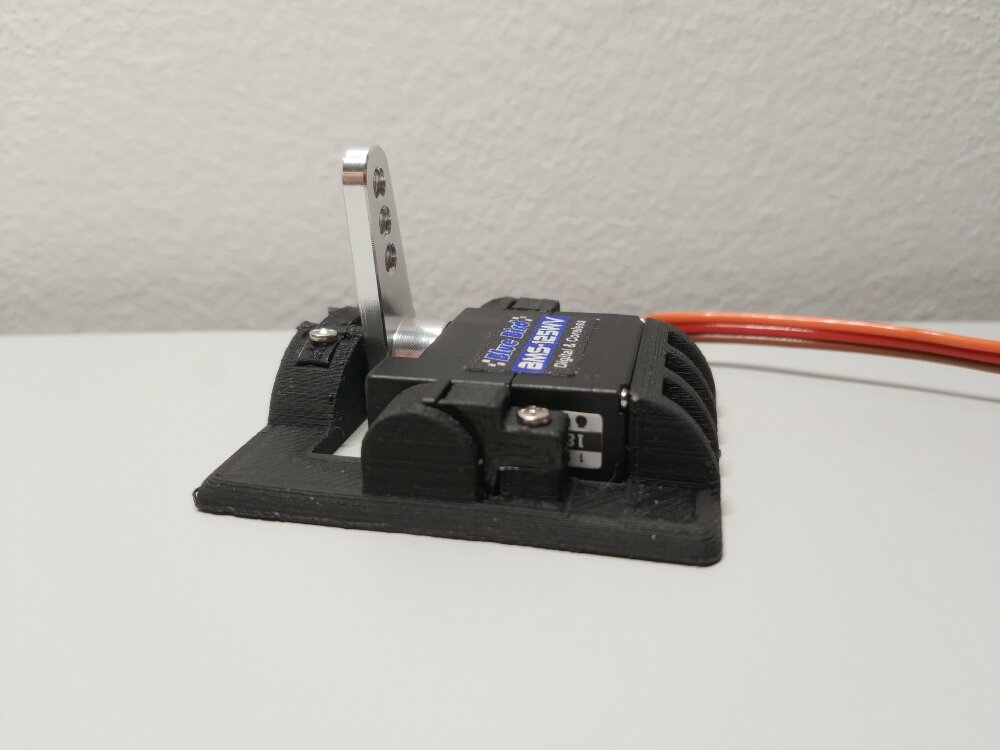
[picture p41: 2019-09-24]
assembly/p08-assembly.jpg

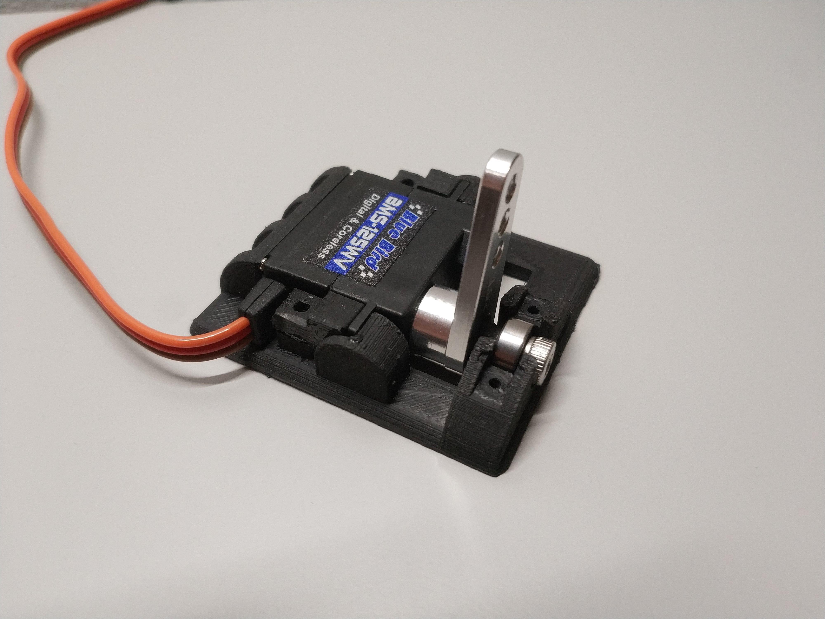
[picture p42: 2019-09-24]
assembly/big/p05-assembly.jpg

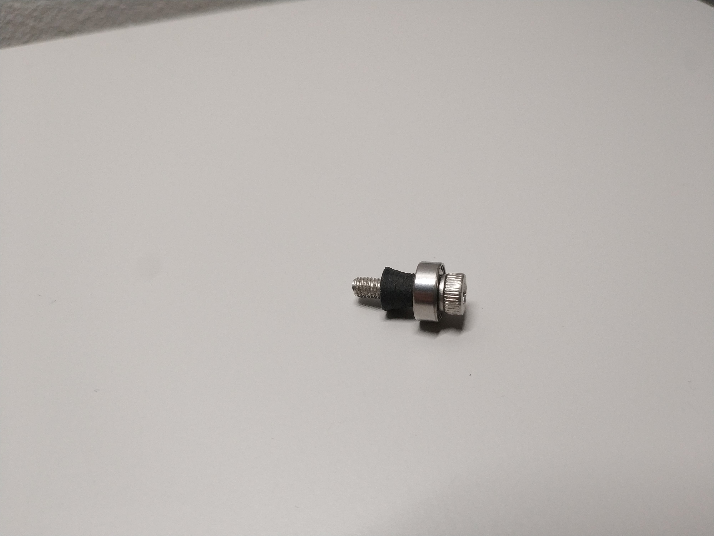
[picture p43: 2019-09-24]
assembly/big/p02-assembly.jpg

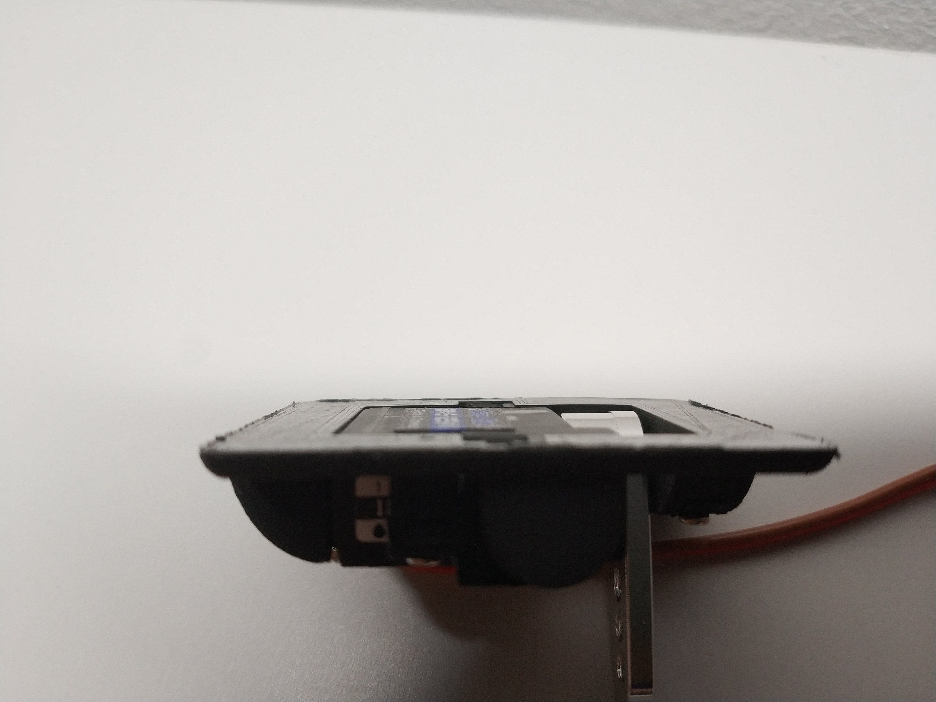
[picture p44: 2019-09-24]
assembly/big/p09-assembly.jpg

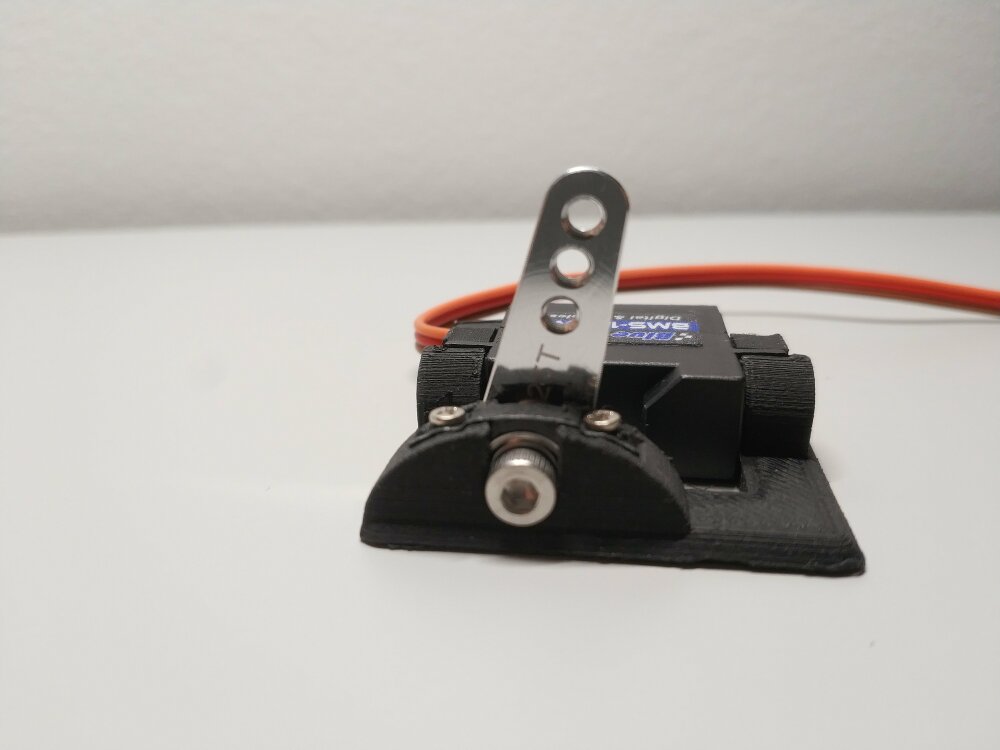
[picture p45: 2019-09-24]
assembly/p07-assembly.jpg

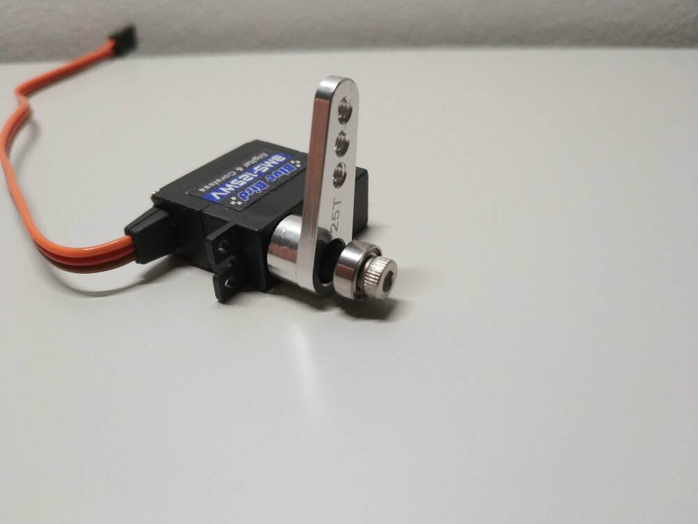
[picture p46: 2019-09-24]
assembly/p03-assembly.jpg

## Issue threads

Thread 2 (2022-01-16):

MKS HV6110 wing servo frame

cozzierich, 2022-01-16:
I see you have servo frames for the MKS-6100 and was wondering if you could add servo frames for the MKS-HV6110.

Thank you.

guillaumef, 2022-01-16:
Hi,

DS6100 and HV6100 have the same dimensions.
http://www.mks-servo.com/image/Glider%20Servo/Dimension/DS6100_Dimension01.jpg
http://www.mks-servo.com/image/Glider%20Servo/Dimension/HV6100_Dimension.jpg

It was specified in the servo-frame.scad and the homepage here.
/* Servo #0,0    - MKS DS6100 / HV6100                                           */
MKS DS6100 / HV6100

So you can use the DS6100 stls directly.

Enjoy! Put a star the project and talk about it ;-)
Thank you!

Closed 2022-01-16.

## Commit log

2019-09-15 servo ear mods
    [frame-BlueBird-BMS-125WV-all.stl, frame-BlueBird-BMS-125WV-l-bearing.stl, frame-BlueBird-BMS-125WV-no-bearing.stl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]
2019-09-16 bearing shaft enhancements
    [servo-frame.scad]
2019-09-24 some fine tuning
    [servo-frame.scad]
2019-09-24 assembly pictures
2019-09-25 light mode (holes in frame) and closed frame for horizontal ears
    [servo-frame.scad]
2019-09-26 servo kb
    [servo-frame.scad]
2019-09-27 arm thickness and clearance modification
    [frame-MKS-DS6100-all.stl, frame-MKS-DS6100-l-bearing.stl, frame-MKS-DS6100-no-bearing.stl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]
2019-09-27 split configuration file, ovalized bearing holder, full automation for stl generation and animated gifs
    [configuration.scad, frame-BlueBird-BMS-125WV-all.stl, frame-BlueBird-BMS-125WV-l-bearing.stl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]
2019-09-27 last gifs
    [hollow_bearingLR_2.5x6x2.6.png.scad, hollow_bearingLR_2x5x2.5.png.scad, hollow_bearingLR_3x6x2.5.png.scad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]
2019-10-05 add holes for no-ear servo cover
    [servo-frame.scad]
2019-10-05 stl regen - bms-a10* added
    [configuration.scad, hollow_bearingLR_2.5x6x2.6.stl, hollow_bearingLR_2x5x2.5.configuration.scad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]
2019-10-28 Change default configuration arm_thickness for a more common value
    [configuration.scad, servo-frame.scad]
2019-10-30 real example - bms-125wv
